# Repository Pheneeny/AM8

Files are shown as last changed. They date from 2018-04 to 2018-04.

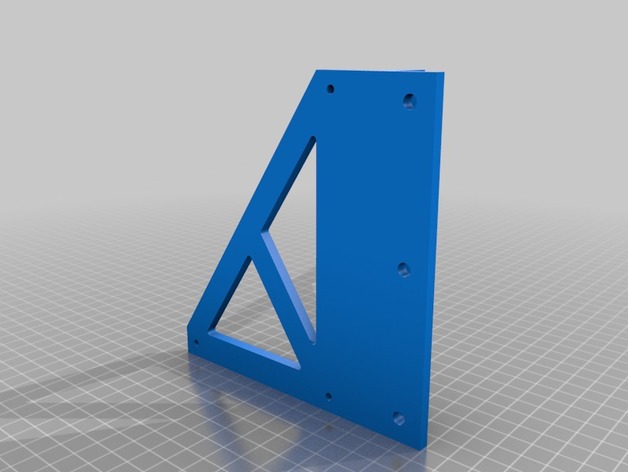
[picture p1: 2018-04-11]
images/0723ebf0788d00d7d7afbb4037fb717d_preview_featured.jpg

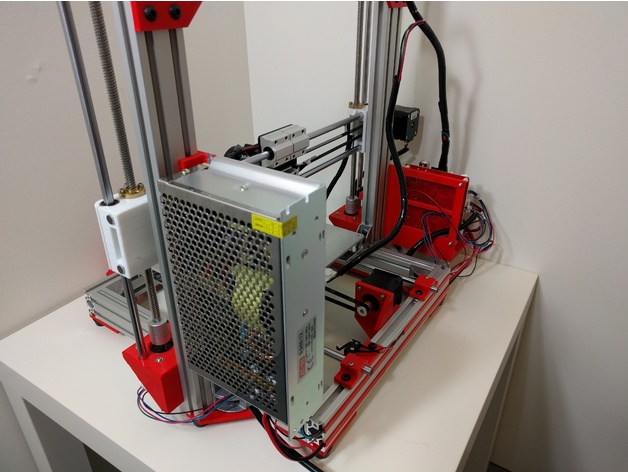
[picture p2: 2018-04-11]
images/4edb620356ea50f0c485873091d36dc9_preview_featured.jpg

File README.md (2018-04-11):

### AM8 - A Metal Frame for the Anet A8

This project aims to build a sturdy aluminum frame for your Anet A8, while re-using as many components as possible to keep costs low. This frame can be built for roughly $55, plus the costs of plastic. 

The BOM.pdf file contains all of the parts you need to buy and where to get them.
The Build_Guide.pdf has the build instructions. 

This frame uses Misumi 2040 aluminum extrusions and aluminum corner brackets for primary frame connections, and printed plastic parts for alignment. 

This project only aims to replace the acrylic frame of the Anet A8. The project was designed and built with a stock Anet A8 in mind, in an attempt to reach the widest audience. Many of the existing mods and upgrades should still be compatible with this new frame, although some upgrades may no longer be needed. 

This project does not address any other issues with the Anet A8. Those issues should still be fixed on their own (Such as the mosfet mod). 

Ideally, your Anet A8 is not your only printer, so that rebuilding it does not leave you without a working printer if something should go wrong with your build. 

Build this at your own risk.

##### Optional Parts
The Anet Board Mount can be printed with or without an 80mm fan mount attached. I recommend mounting a fan to help keep the board cool. Any 80mm computer fan should work. If you are using a fan, please print or buy fan guards to prevent fingers or wires from going into the fan.

##### Additional Parts:
[T-Slot Wire Cover](https://www.thingiverse.com/thing:832077)
[E3D V6 Mount](https://www.thingiverse.com/thing:2316850)
___
##### Update 10/21/17
Fixed broken Misumi links in BOM.
Added shorter bed screws to BOM to avoid interference with Y rod holders.
##### Update 5/13/17
Added E3D V6 Mount link
##### Update 5/6/17
Uploaded fixed STLs for the the following files:
Z_Motor_Mount_Right
Z_Motor_Mount_Left
Y_Motor_Mount
Z_Endstop
Anet_Board_Mount_No_Fan

All of the old files can be found in the old_stl.zip file
##### Update 4/28/17
Added Fusion 360 Design files
##### Update 4/22/17
Added missing link for M5 Square nut to BOM.

# [Thingiverse mirror](https://www.thingiverse.com/thing:2263216)

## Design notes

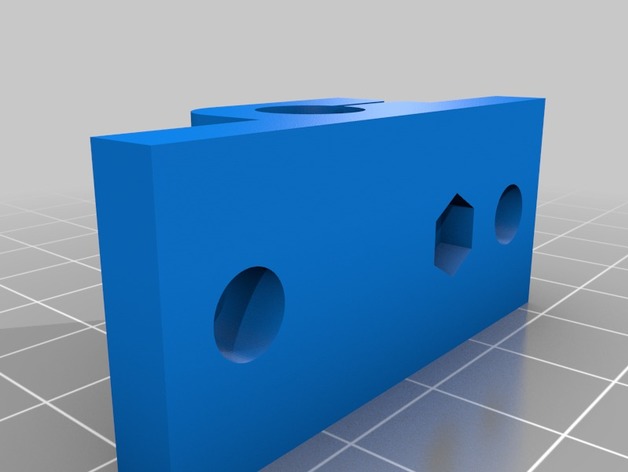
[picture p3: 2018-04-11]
images/45764073fbc0add2e942828fd61ef08d_preview_featured.jpg

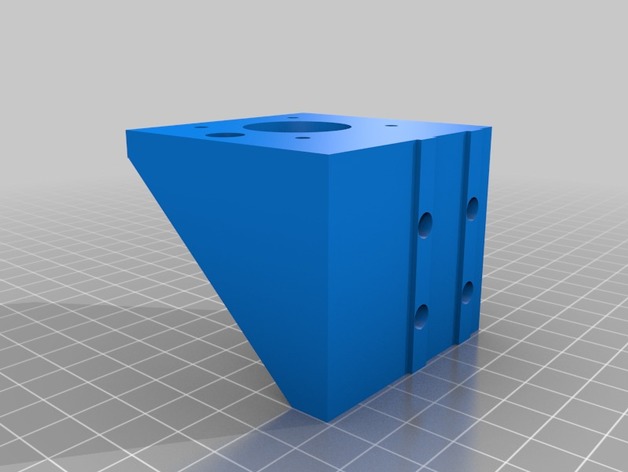
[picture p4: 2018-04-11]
images/f489a5f989ccbbf9bacde3c97e97e00a_preview_featured.jpg

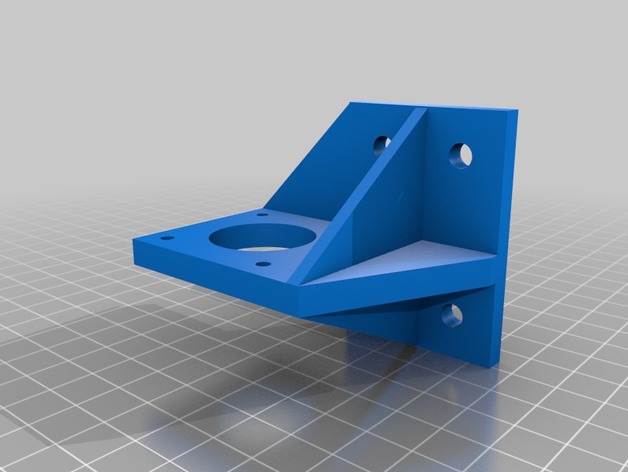
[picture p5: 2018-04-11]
images/10357ed140a1ebb7b7c83b60e00c0d15_preview_featured.jpg

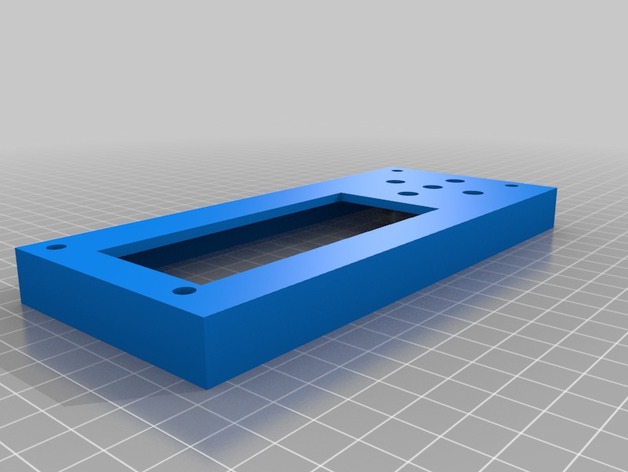
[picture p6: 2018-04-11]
images/1ac8dad0431415d9a7ae9dcd8d58470f_preview_featured.jpg

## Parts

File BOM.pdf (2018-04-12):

AM8 BOM

Page 1

Item | Qty | Unit Cost Total Cost Link | Notes
Extrusions
340mm 2040 Misumi HFS5-2040-340 | 2 | $3.63 | $7.34 | Side extrusions for the Y axis
313mm 2040 Misumi HFS5-2040-313 | 3 | $3.38 | $10.14
440mm 2040 Misumi HFS5-2040-440 | 2 | $4.75 | $9.50 | Vertical Z extrusions
Brackets
HBLFSNF5 Corner Bracket | 12 | $0.63 | $7.56
Hardware
M5x10 Button Head Socket Cap Screw | 100 | $0.09 | $8.99
M5x10 Socket Head Cap Screw | 8 | $0.14 | $1.12 | Used for Z axis motor mounts
M5x16 Socket Head Cap Screw | 6 | $0.25 | $2.25 | Used for rubber feet connections
M5x.8 Square Nut | 110 | $0.04 | $4.40
M3 Washer | 8 | $0.02 | $0.16
M3x25 Flat Head Machine Screw | 4 | $0.05 | $0.20
Misc
Rubber Feet 10 pack | 1 | $6.26 | $6.26 | Only need 6

Total
| | | $57.92

With MrMetric.com going out of business, I am finding alternative sourcing for the parts. If I have completely replaced the MrMetric link, that means they no longer have the part in stock (And won’t be getting it again). If an item has multiple links, it means the item was still available from MrMetric at the time of edit but an alternative link is being provided for whenever they run out of stock.
For full disclosure, the Amazon links are affilliate links, and I may earn a small commision from Amazon if you purchase the products through that link (at no extra cost to you).

https://us.misumi-ec.com/vona2/detail/110302684350/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

https://us.misumi-ec.com/vona2/detail/110302684350/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

Front, back, and cross member at the top of the Z axis.
https://us.misumi-ec.com/vona2/detail/110302684350/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

https://us.misumi-ec.com/vona2/detail/110300437260/?Inch=0

https://www.amazon.com/dp/B073H3GBJM/?tag=am8-20

93 are actually needed, but 100 gives you a significant discount and a few extras just in case. http://www.mrmetric.com/M10089
OR
https://www.amazon.com/dp/B00I0X8VQY/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
OR
https://www.amazon.com/dp/B019ZXUSY0/?tag=am8-20http://www.mrmetric.com/M60753

http://www.mrmetric.com/M30799

Shorter screws for bed leveling to avoid interference with rod holders.

https://www.amazon.com/dp/B008LTY1NO/?tag=am8-20

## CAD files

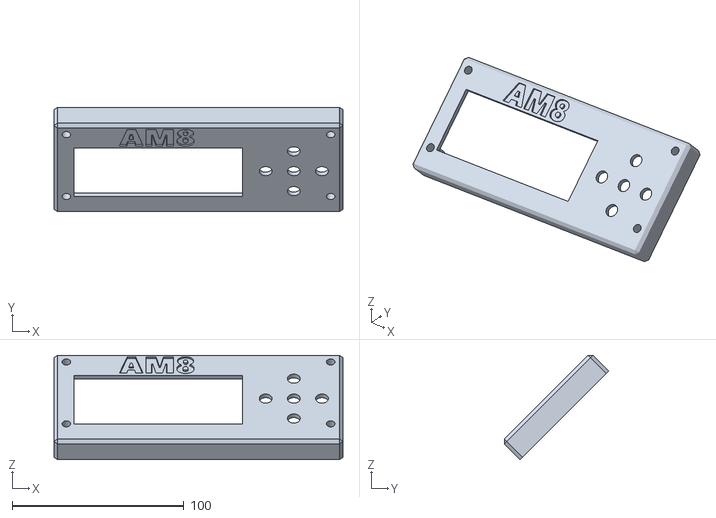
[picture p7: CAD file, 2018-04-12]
STLs/1_LCD_Case_Top_V2.stl
168.4 x 60.8 x 60.8

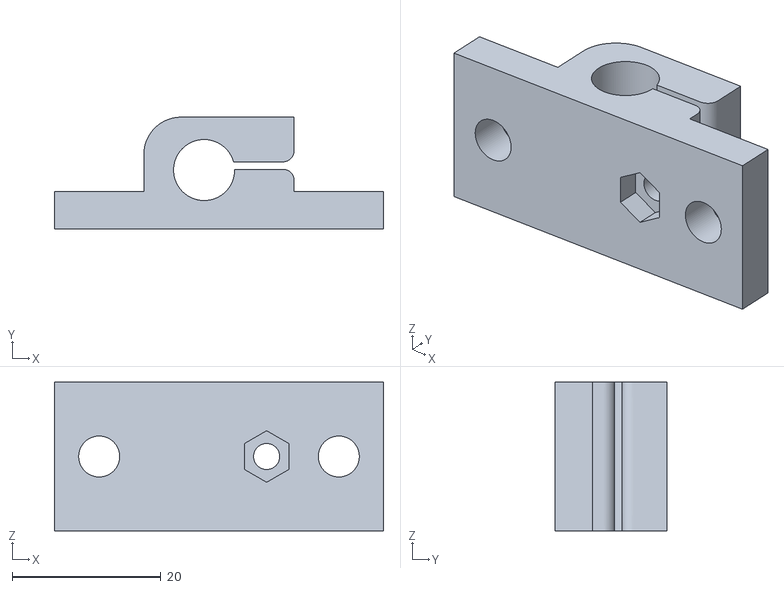
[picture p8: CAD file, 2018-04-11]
STLs/3_Y_Rod_Holder.stl
44.2 x 15.0 x 20.0

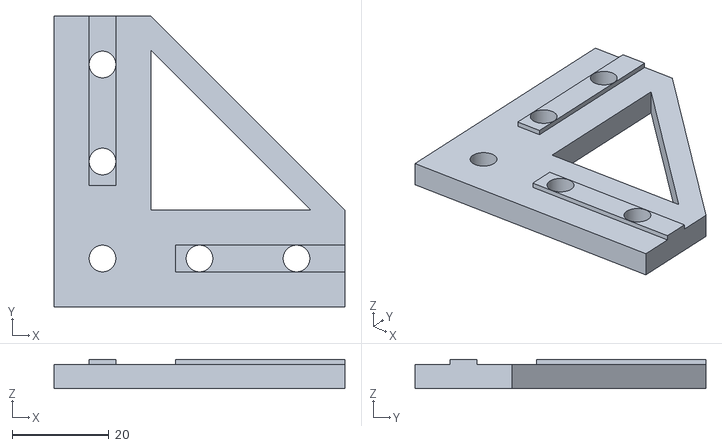
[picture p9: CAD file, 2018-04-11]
STLs/4_Bottom_Corner_Plate.stl
60.0 x 60.0 x 6.00

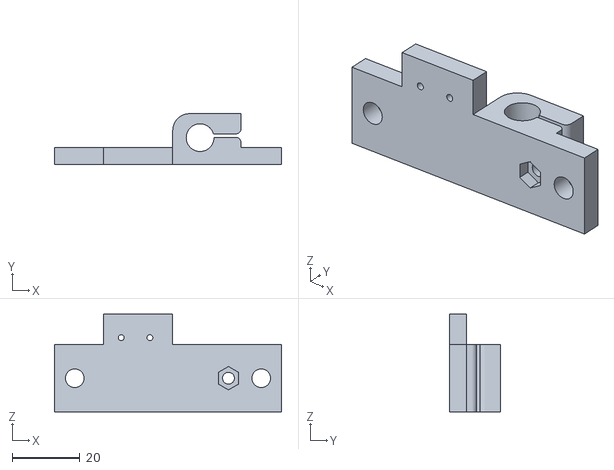
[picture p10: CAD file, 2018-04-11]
STLs/1_Y_Rod_Holder_With_Endstop.stl
67.2 x 15.0 x 29.0

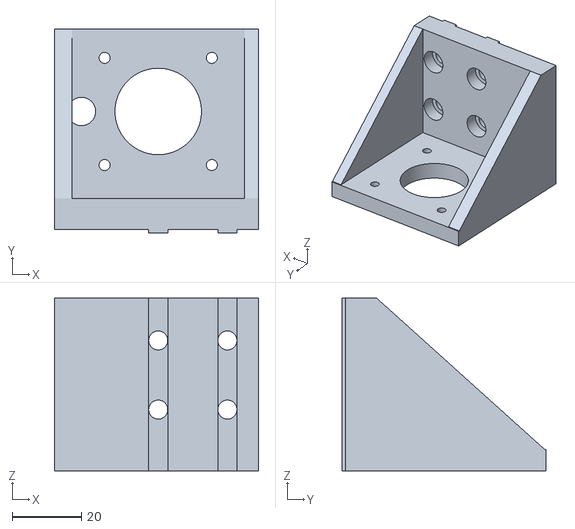
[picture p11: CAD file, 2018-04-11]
STLs/1_Z_Motor_Mount_Left.stl
59.0 x 59.0 x 50.0

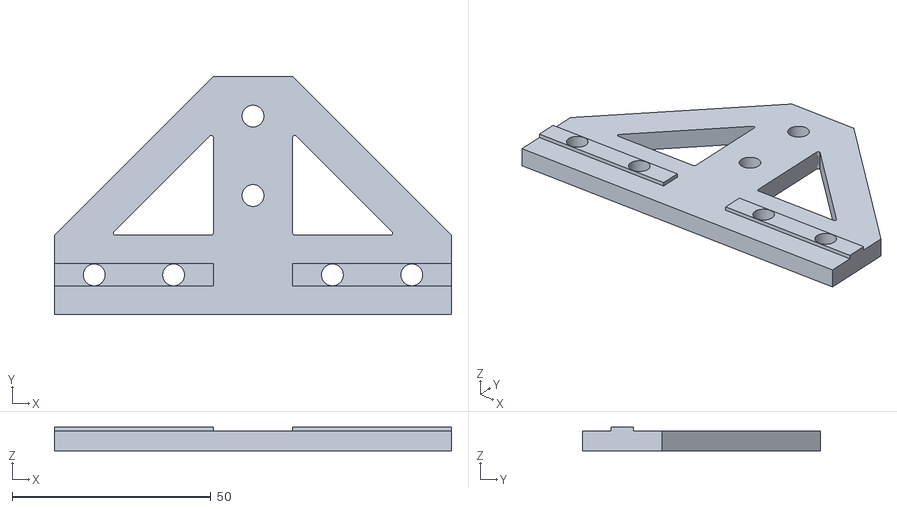
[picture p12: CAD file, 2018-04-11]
STLs/2_Bottom_Tee_Plate.stl
100.0 x 60.0 x 6.00

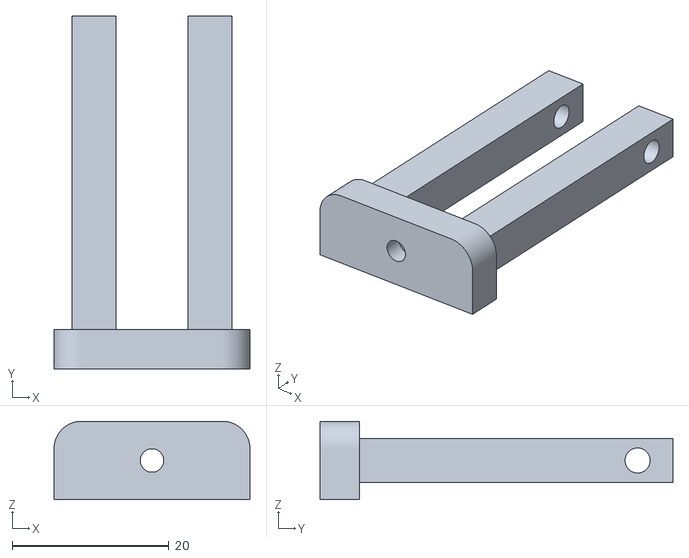
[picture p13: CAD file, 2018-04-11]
STLs/1_Y_Belt_Tensioner.stl
25.0 x 45.0 x 10.0

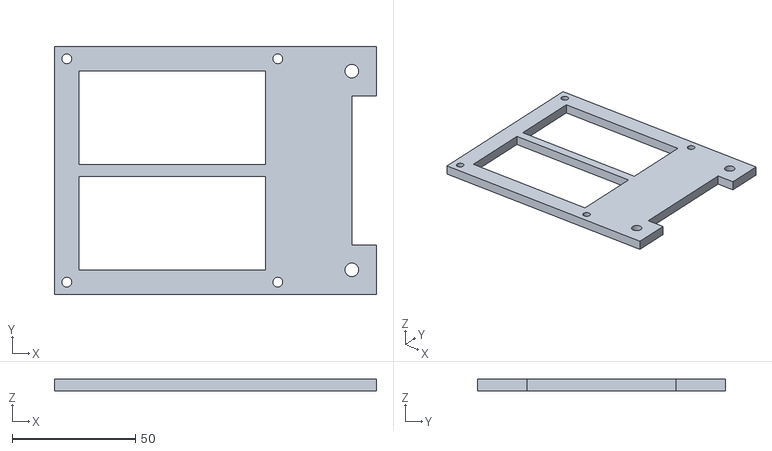
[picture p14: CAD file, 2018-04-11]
STLs/Anet_Board_Mount_No_Fan.stl
130.5 x 100.5 x 5.00

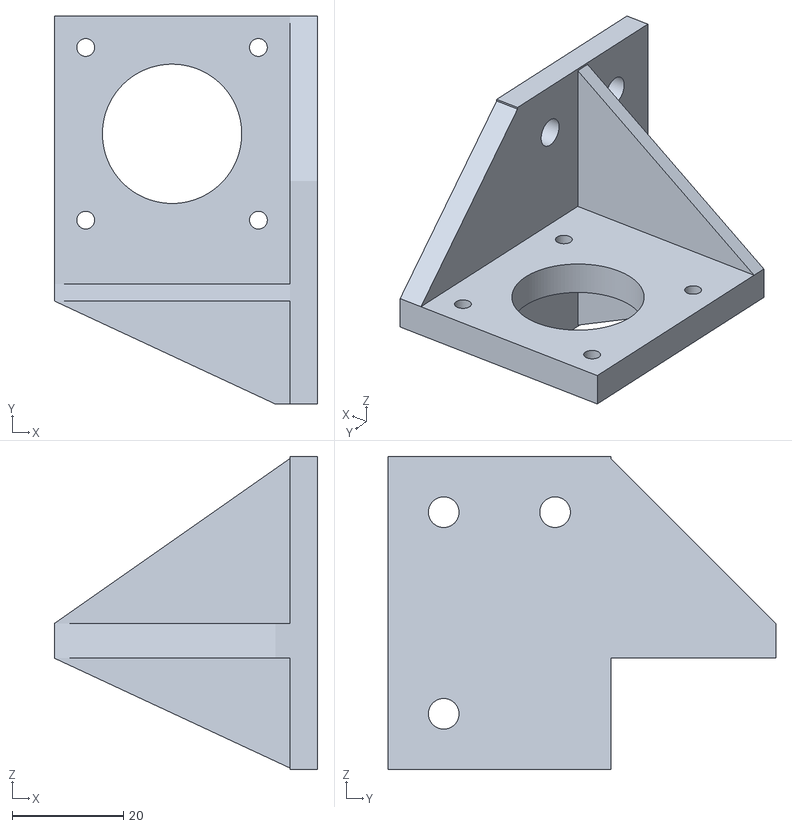
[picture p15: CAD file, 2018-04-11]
STLs/1_Y_Motor_Mount.stl
47.3 x 69.6 x 56.2

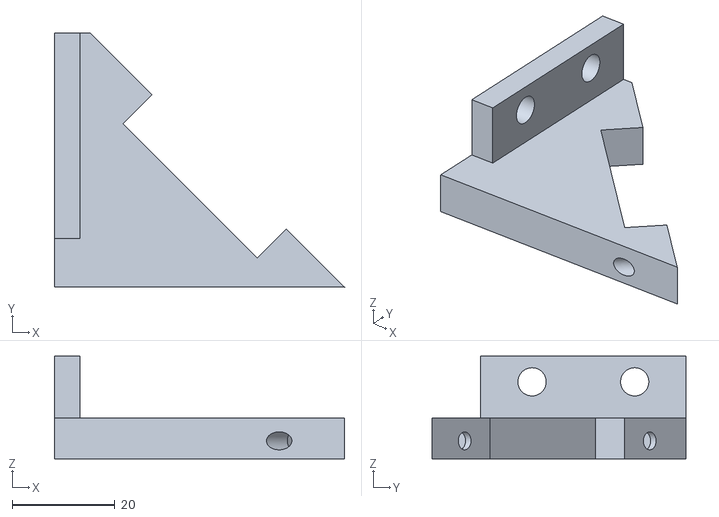
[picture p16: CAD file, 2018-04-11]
STLs/1_LCD_Base_Left.stl
56.5 x 49.5 x 20.0

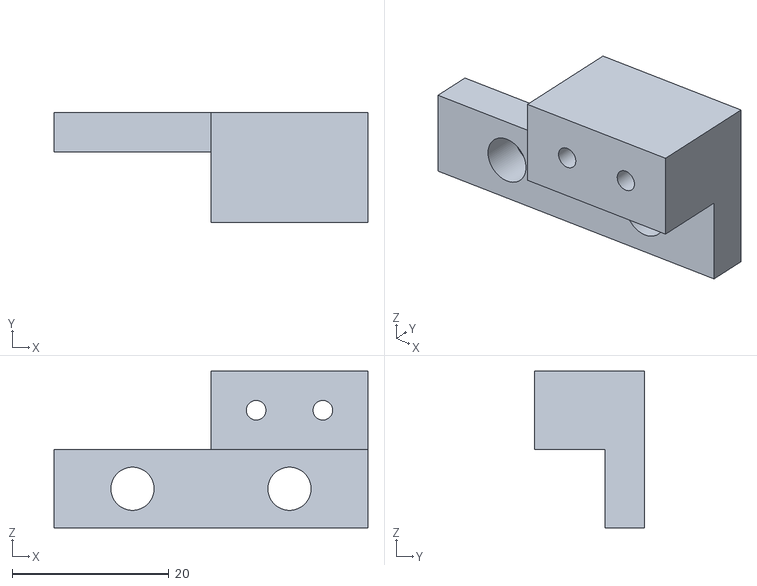
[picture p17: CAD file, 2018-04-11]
STLs/1_Z_Endstop.stl
40.0 x 14.0 x 20.0

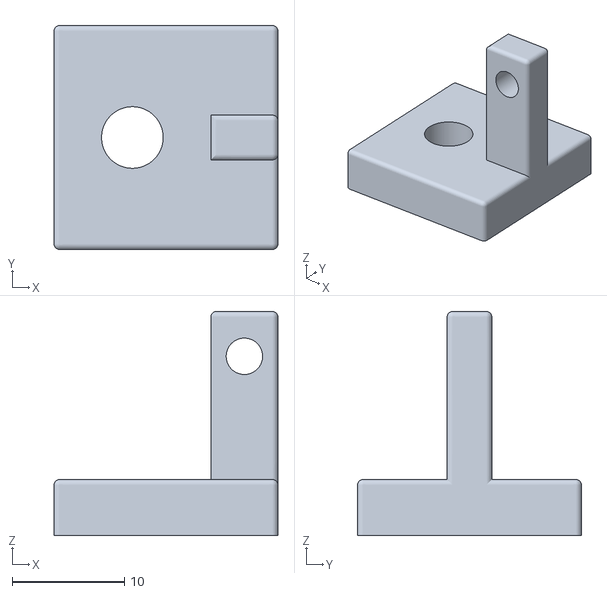
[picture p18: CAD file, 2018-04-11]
STLs/1_Wire_Holder.stl
20.0 x 20.0 x 20.0

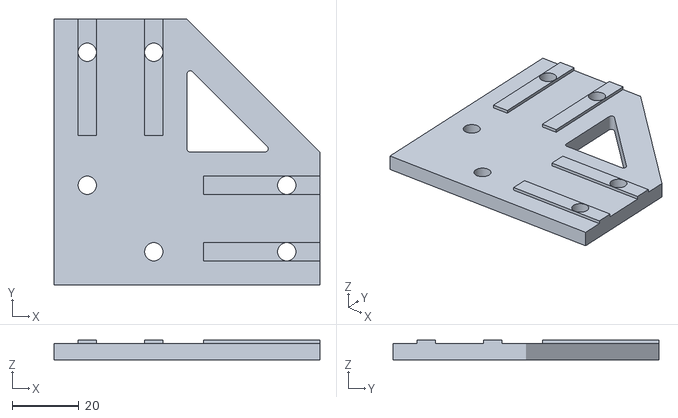
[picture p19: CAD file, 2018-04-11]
STLs/2_Top_Corner_Plate.stl
80.0 x 80.0 x 6.00

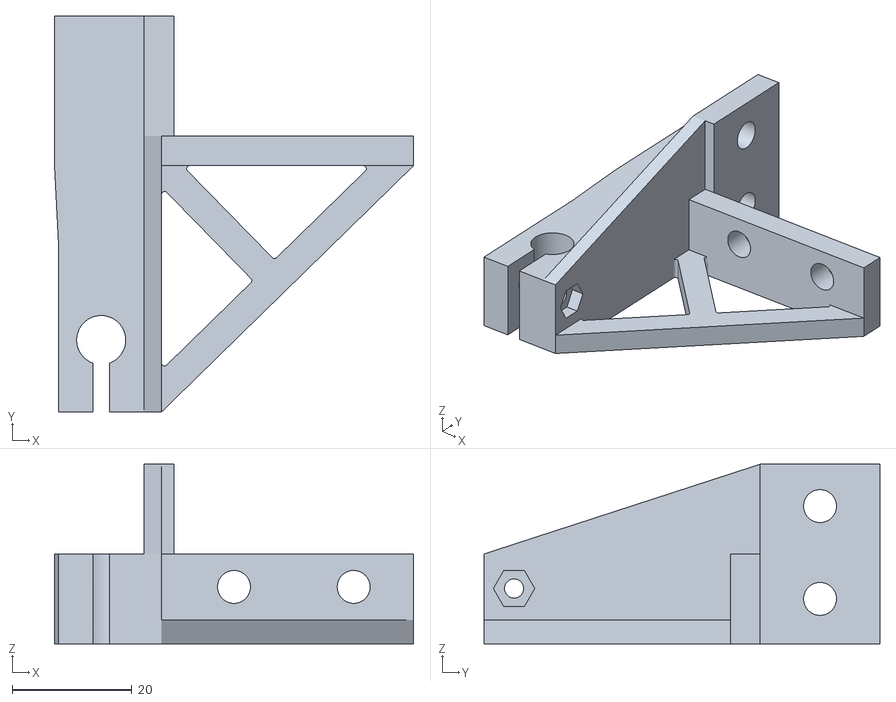
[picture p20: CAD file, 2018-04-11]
STLs/1_Z_Rod_Holder_Right.stl
60.0 x 66.1 x 30.0

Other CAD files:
STLs/1_Z_Motor_Mount_Right.stl
STLs/1_LCD_Base_Right.stl
STLs/1_Y_Belt_Block.stl
STLs/1_PSU_Mount.stl
AM8.f3d
STLs/1_Z_Rod_Holder_Left.stl
STLs/Anet_Board_Mount__With_Fan.stl

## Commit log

2018-04-11 Initial import. Mirror of Thingiverse project
    [1_LCD_Base_Left.stl, 1_LCD_Base_Right.stl, 1_LCD_Case_Top.stl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]
2018-04-12 Updated BOM, Added LCD Case V2
    [1_LCD_Case_Top.stl, 1_LCD_Case_Top_V2.stl]
